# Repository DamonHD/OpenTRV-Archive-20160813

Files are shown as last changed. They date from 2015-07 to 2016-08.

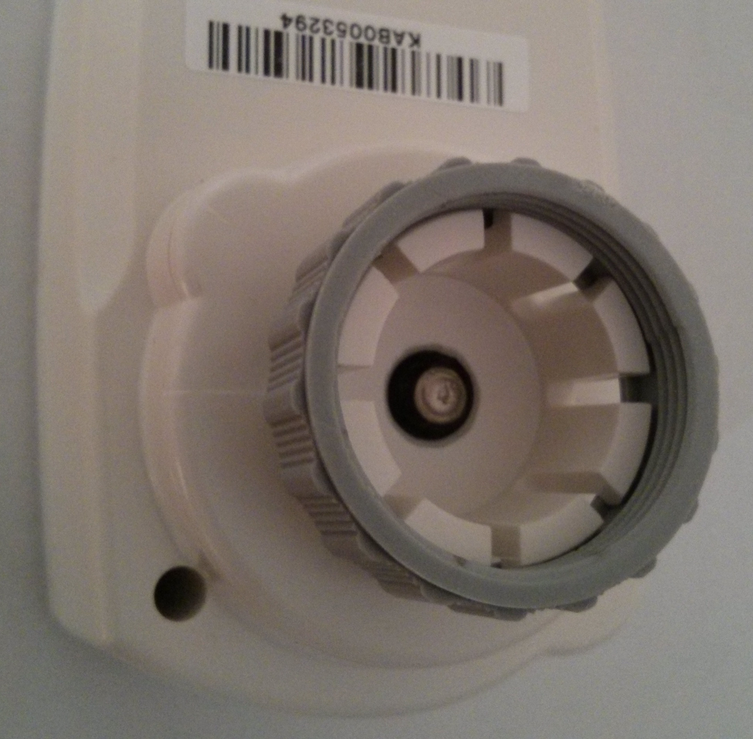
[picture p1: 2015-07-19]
docs/maker-fair-sandown-park/sources/rtrv.jpg

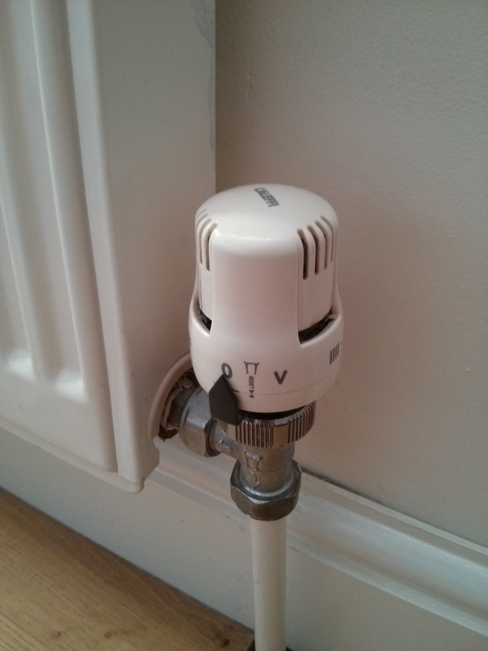
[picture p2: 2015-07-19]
docs/maker-fair-sandown-park/sources/IMG_20131211_112003.jpg

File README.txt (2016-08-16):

WARNING: AS OF 2016/08/13 THIS IS A READ-ONLY ARCHIVE/SNAPSHOT WITH HISTORY

See https://github.com/opentrv/OTWiki/wiki/Repo-Restructure-2016-08-13
for how the content has been refactored.

This is the OpenTRV (Open-Source Thermostatic Radiator Valve) project.

See http://www.earth.org.uk/open-source-programmable-thermostatic-radiator-valve.html for more.

Contains software and hardware elements.

Note that the content of this project is available under a permissive licence,
Apache 2.0 or (Solderpad 0.51 for hardware elements) unless otherwise stated,
and is provided supplied AS-IS with no warranties of any kind.

Fragments of contributed code, libraries, etc, within here may have their own licences,
in which case that should be explicit in each case.

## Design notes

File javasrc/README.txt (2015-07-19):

Installation instructions

To install on a Raspberry Pi, you will need to install the following
packages first:

$ sudo apt-get install librxtx-java
$ sudo apt-get install libjson-simple-java

The latest raspbian release (2015-02-06) comes with Oracle JDK 8 by default,
which should work. If you prefer 7, you can install that instead:

$ sudo apt-get install oracle-java7-jdk

Add the latest soft link in /usr/lib/jvm
$ cd /usr/lib/jvm
$ ln -s ./jdk-8-oracle-arm-vfp-hflt latest

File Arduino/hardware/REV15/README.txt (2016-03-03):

REV15+

A set of modular processor and sensor boards that can be stacked on top of each other as needed. These boards would have the I2CEXT connector, located in a common position.

The boards should include:
- A processor board.
- A power supply board.
- A radio board.
- Various sensor boards.

Specifications:

Physical layout:
- 5 cm x 5 cm form factor
- Standard positioning of 4 screw holes (as on REV2).
- Standoffs to work with connectors, long lead connectors.
- The I2CEXT connector as defined in https://github.com/DamonHD/OpenTRV/blob/master/standards/I2CEXT/tech-specs/201602-AVR-I2CEXT-connector.txt

Individual boards:
- Processor board (REV15):
    - Atmega328p
    - Watch xtal/resonator
    - Photodiode
    - Status LED
- Power supply board (REV16*):
    - Micro USB connector.
    - 2xAAA Battery connector (as on REV11)
    - 3.3 V regulator
- Radio board (REV17*):
    - Pads and connections for a single RFM23B or pin compatible RFM69.
    - Not backwards compatible with RFM22.
    - Decide on antenna.
- Sensor boards:
    - Temp/humidity (REV18*)
- More TBD. Suggestions include:
    - CO2 sensor board (sensor TBD).
    - PIR
    - CO
    - PMx
    - VO

* To be renamed.

Dir structure:
./
    - rev15.sch
    - rev15.brd
    - README.txt
    - CHECKLIST.txt
    + DRU+CAM/
    + gerbers/ *THIS CONTAINS GERBERS FOR ALL BOARDS*
    + REV16/
    + REV17/
    + REV18/

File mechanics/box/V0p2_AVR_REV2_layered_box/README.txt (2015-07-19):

Built around standard 5cm x 5cm board (with M3/3mm corner mounting holes, 1mm from edge).

M3 bolts with 30mm shank and full-height (2.4mm) nuts should then be correct length
with 0.5mm recess at top 30mm case height.

4 layers totalling 30mm:

0. (11mm) Base + screw mounts and lower collar with micro-usb cut-out.
1. (6mm) Top collar with power and boiler wire cut-outs.
2. (30.5mm-others) Spacer to provide clearance for front-panel items (and possibly to match bolt length!).
3. (3mm) Front panel with supports for button/LED/LDR board and cut-outs for those 4 items.

Good source of fasteners: www.westfieldfasteners.co.uk

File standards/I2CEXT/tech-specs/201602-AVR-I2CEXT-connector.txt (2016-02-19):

The OpenTRV project licenses this file to you
under the Apache Licence, Version 2.0 (the "Licence");
you may not use this file except in compliance
with the Licence. You may obtain a copy of the Licence at

http://www.apache.org/licenses/LICENSE-2.0

Unless required by applicable law or agreed to in writing,
software distributed under the Licence is distributed on an
"AS IS" BASIS, WITHOUT WARRANTIES OR CONDITIONS OF ANY
KIND, either express or implied. See the Licence for the
specific language governing permissions and limitations
under the Licence.

Author(s) / Copyright (s): Damon Hart-Davis 2014--2015

REVISIONS

2015/11/27: Revision 6 proposal, New I2CEXT design.
2014/09/14: Revision 5, adding some more details of location and form.
2014/09/08: Revision 4, allowing 4k7 for RX/TX serial for common values.
2014/09/08: Revision 3, note that the nIRQ and nSC lines can be left unconnected on some board variants.
2014/09/04: Revision 2, 14-pin connector, added nINT and nSC2 after dev mailing list suggestions
2014/09/03: Revision 1, 12-pin connector

Aim:

Trying to develop a simple I/O extension/shield system for OpenTRV to add more sensors (etc) easily.

Also this should allow an easy bridge to other systems such as RPi / BB / etc.

This must be simple and small and cheap enough to use in hobby / dev / prod environments and allow (in priority order):

1) I2C expansion.
2) In-Circuit Programming of AVR.
3) One-Wire expansion.
4) Serial off-take, eg for CLI interaction.

The connection should ideally be keyable or at least not cause instant destruction if reversed for example.

New Suggestion:

20 way (2x10) pin stackable

0.1 " pitch

Following pin pattern:
  PIN 1| PIN 2
MISO * .. * 3V3 (Vcc)
 SCK * .. * MOSI
nRST * .. * GND
 N/P X .. X N/P
 SCL * .. * GND
 SDA * .. * GND
nIRQ * .. * N/C
 nSS * .. * TX
  DQ * .. * RX
 PIO * .. * RTS

1) Pins 1-6 are standard AVR ICSP connections
2) 7-8 have no pins. This:
    a) Gives space for an IDC connector when programming with ICSP.
    b) Allows for a keyed 20 pin IDC.
3) 10-20 (even only) are standard FTDI connections (as on cable from RS components)
4) 9 & 11 are I2C connections.
5) 13 is a generic interrupt line to the AVR.
6) 15 is a slave select line in case of an external SPI peripheral. NOT the one connected to an on board radio module (if present).
7) 17 is a one wire serial connection.
8) 19 is a peripheral power enable line.

a) N/C means No Contact.
b) RX and TX are protected by 4K7 series resistors from AVR.
c) nRST (input to main board) is active low and is pulled up to 3V3/Vcc with 4k7--10K series resistor at AVR.
d) SCL and SDA are pulled up at AVR with 4K7 resistors to 3V3/Vcc.
e) 3V3 can be anywhere from 1V8 to 3V6 absolute; 2V to 3V6 operating.
f) nIRQ (input to main board) is active low and is pulled up to 3V3/Vcc with a 10K--47K nominal resistor and a 1K series resistor: this should be driven with open collector/drain driver only.
g) nSS (output from main board) is the active low select for an SPI device on the bus,
h) The nIRQ and nSS lines can be left unconnected unless the main board variant explicitly supports them.
i) N/P means No Pin.
j) PIO is connected to the IO_POWER_UP pin (via a resistor?) and is used for switching external sensors on
k) RTS is connected to nRST via a 100nF capacitor

Features:

1) Top 6 pins can be used directly with 6-pin AVR programmer.
2) 6 pins down the side can be used directly with a 6 pin FTDI cable (but must be powered from a different source)
3) When used with properly keyed IDC, cable cannot be inserted the wrong way.
4) The connector must be laid out as a single unit on the PCB ie. as a single 20 pin header
5) The connector may be populated by a 6 pin and a 12 pin header

Current:

14-way (2x6) pin stackable (pins or socket on board, suggestions please, RPi is pins).

0.1" pitch to be easy for DIY shields, eg with Veroboard as I just did for my RPi.

Following pin pattern:

MISO * .. * 3V3 (Vcc)
 SCK * .. * MOSI
nRST * .. * GND
nIRQ * .. * nSC
 SCL * .. * SDA
  RX * .. * TX
 N/C * .. * DQ

a) N/C means No Contact and can be used to key the connector.
b) RX and TX are protected by 10k series resistors from AVR.
c) nRST (input to main board) is active low and is pulled up to 3V3/Vcc with 4k7--10K series resistor at AVR.
d) SCL and SDA are pulled up at AVR with 4K7 resistors to 3V3/Vcc.
e) 3V3 can be anywhere from 1V8 to 3V6 absolute; 2V to 3V6 operating.
f) nIRQ (input to main board) is active low and is pulled up to 3V3/Vcc with a 10K--47K nominal resistor and a 1K series resistor: this should be driven with open collector/drain driver only.
g) nSC (output from main board) is the active low select for an SPI device on the bus,
h) The nIRQ and nSC lines can be left unconnected unless the main board variant explicitly supports them.

Features:

1) Top 6 pins can be used directly with 6-pin AVR programmer.
2) Rest of pins carry I2C (SDA, SCL), OneWire (DQ) and serial (RX, TX, protected by 10k series resistors)
3) If entire connector rotated boards unlikely to be destroyed instantly.

Bit more on (3): RX and TX are safe to short to GND or 3V3 or anything else, nRST safe to short to either rail, DQ/SCA/SCL safe to short to GND.

Connector form/style and location, and constraints:

1) Should be near board edge but not in corner for REV2-style 5x5 box.
2) Should be placed prob near edge for easy dev access with 3D-printed board.
3) Should allow USB micro socket to go back in its REV2 position if possible.
4) Should allow I2CEXT board on 5x5 footprint to also be RPi HAT board.
5) Must not be single-source nor expensive nor anywhere near end-of-life.

Some agreed details:

a) Male 7x2 0.1" pitch connector like top part of Raspberry Pi A/B/B+ GPIO connector, with pins above the board (component side).
b) Stacked board to have female connector below the board with extra long pins up.
c) Location on standard 5cm x 5cm OpenTRV board:
   6.35mm (left) x 2.375mm (down) from top left corner of board to centre of top-left pin (3V3)
   with the connector running left to right
   with pins pointing vertically away from the plane of the board towards the viewer.

Note: see alternatives such as http://www.tag-connect.com/ for SPI/ICP part.

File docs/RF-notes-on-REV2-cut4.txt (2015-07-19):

2014/07/03: discussing possible CE-stamp RF problems on IRC...

[21:40] mikestir    yes looking at it it's not great in terms of ground plane, but it's not exactly a speed demon
[21:41] mikestir    I can't see it being a big problem
[21:41] mikestir    also the rf track isn't
[21:41] mikestir    and the tracks are _still_ unnecessarily thin
[21:41] mikestir    I've given up telling you about that though
[21:42] DamonHD I did try to widen them a little but we were having trouble routing.
[21:42] DamonHD And all the supply tracks are now much wider than they were in their own net class.
[21:42] Boelle_DK   *me hides*
[21:42] DamonHD And we're way above iTEAD and PMS limits.
[21:43] mikestir    the ground plane thing just needs some stitching vias so you don't have it cut up into slots
[21:43] mikestir    slots are bad - they act as antennas
[21:43] DamonHD Doesn't that risk ground loops?
[21:43] mikestir    no - you have a ground loop as it is
[21:43] mikestir    look at that thin section of ground on the top layer that goes all the way around the bottom edge
[21:44] mikestir    if you have narrow sections like that and you can't stitch it you need to make sure there's a break at one end
[21:45] DamonHD So stitching / multiple routes is OK.
[21:45] DamonHD ?
[21:45] mikestir    yes
[21:45] DamonHD OK.
[21:45] DamonHD Good to know. Thanks.
[21:45] mikestir    what you don't want is a pair of ground tracks on either side with a via at each end
[21:45] mikestir    if you stick vias all the way along you don't have a loop any more
[21:46] mikestir    the vias and the tiny sections in between have such low resistance and inductance that they cease to matter
[21:47] mikestir    your antenna track should really be designed as a coplanar waveguide with stitching vias along the adjoining ground plane, but it's so short you probably don't need to care about that - what you have is probably fine

[21:47] DamonHD Good!
[21:48] mikestir    http://www.mike-stirling.com/gallery3/index.php/HAB/DSC_2396
[21:48] mikestir    look at the rf layout on that

[21:48] mikestir    that could probably use more stitching vias but I wanted to be kind to the fab, and it works fine

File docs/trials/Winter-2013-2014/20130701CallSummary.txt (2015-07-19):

DHD20130701

Summary of 09:30 telephone conference call today between:
Prof Ruth Rettie (RR) http://www.smartcommunities.org.uk/
Dr Kevin Burchell (KB) http://www.smartcommunities.org.uk/
Damon Hart-Davis (DHD) OpenTRV

DHD gave a brief summary of how the OpenTRV device behaves (eg FROST/WARM/BAKE modes and LEARN),
and explained that it had some additional optional anticipatory 'smarts' that could be used/disabled.

DHD is very keen to get some sort of objective metrics to DECC by end of 2013/2014 winter
to help DECC decide ASAP if worth pursuing zoned smart heating with market incentives etc, etc.

RR suggested that we wouldn't have enough people or time for a full controlled trial
getting good estimates of energy savings, partly because interacting with householders
(eg just talking to them, or collecting gas meter reading)
is slow and expensive and distorts results.

We agreed that we want to have 'normal' people in the trial,
since the aim of OpenTRV is to make energy saving (and decent comfort)
simple/easy (no complex controls/programming) for non-techie non-energy-fanatics,
with relatively little explicit interaction with their heating system.

DHD would also like to include OpenTRV and SuperHome people in the trial,
at least on the side, as OpenTRV should also work for the energy-aware
and/or energy-efficient homes.

RR suggested that we doing a small rolling trial and not expect too many hard numbers,
looking first to improve the ergonomics and to test people's reactions to OpenTRV
in a small set of homes, eg including KB's.  Do people like it?  Do they use more heating?

(This initial set/period might be DHD + KB + BG + BH + maybe one or two others.) 

This can be started before winter proper to test the controls,
but raising the programmed temperature thresholds.

Then maybe we rope in a few of the Smart Communities participants.

DHD would still like to look for a drop in kWh/HDD after OpenTRV installation,
eg in households doing monthly or weekly gas meter readings.

(We might possibly expand to another 5--10 households for the second period?)

RR suggested that the way to take this forward might be with TSB
(Technology Strategy Board) money with a firm to commercialise
one version of OpenTRV (which the permissive licences are meant to facilitate).

We might also talk to Alex at Southampton.

We'll get the first phases going and tighten up subsequent trial design
as we go along, but keeping an eye on getting objective metrics whenever possible.

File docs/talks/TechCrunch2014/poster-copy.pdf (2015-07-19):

£100 per home is our target to fix it

In passing we have created an open, cheap, reliable, low-power

Cheap as chips can be
it must be IoT
(in a speech bubble,
something more
pithy?)

£6bn Is needlessly paid to energy companies in the UK annually

UK houses extant

in 2050 26.5m

OpenTRV
From Rads to (IoT Data) Riches
60%

# half wasted!

of typical UK home energy bill and carbon footprint*
is for space heating
which is
as much as

with radio, security,
and even energy harvesting under development,
for fit-and-forget, cheap-as-chips!

*10% of UK footprint, 8% of EU

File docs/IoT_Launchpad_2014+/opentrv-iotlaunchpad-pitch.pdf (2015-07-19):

w | opentrv.org.uk
t | @opentrv
e | opentrv@opentrv.org.uk

# openTRV

# sensors and infrastructure cheap 'n' easy Damon Hart-Davis

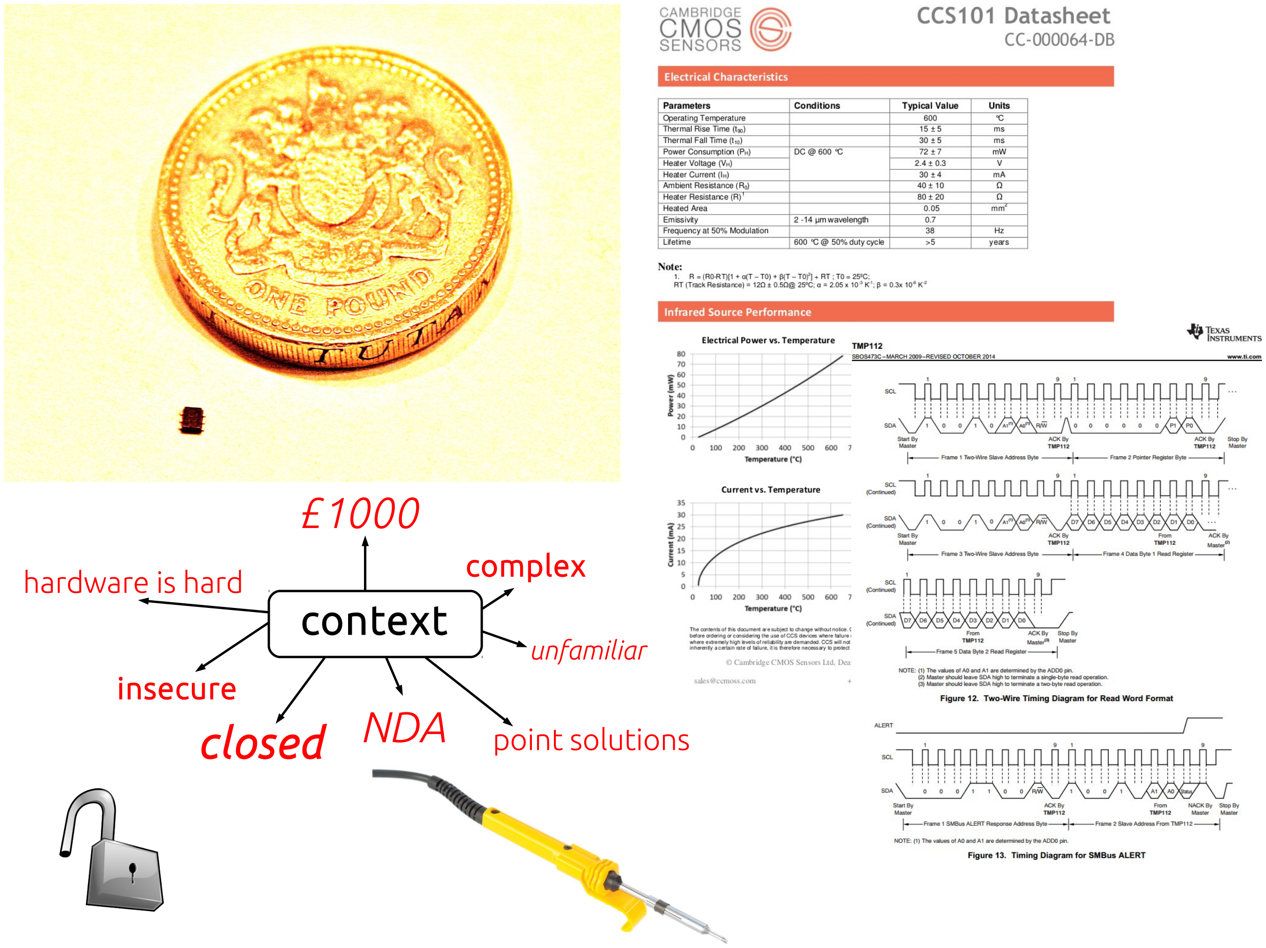
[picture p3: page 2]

## context

insecure

hardware is hard

## closed

£1000

complex

NDA point solutions

unfamiliar

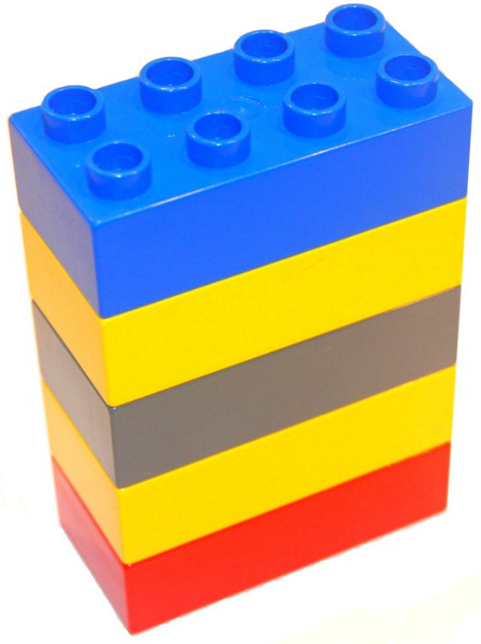
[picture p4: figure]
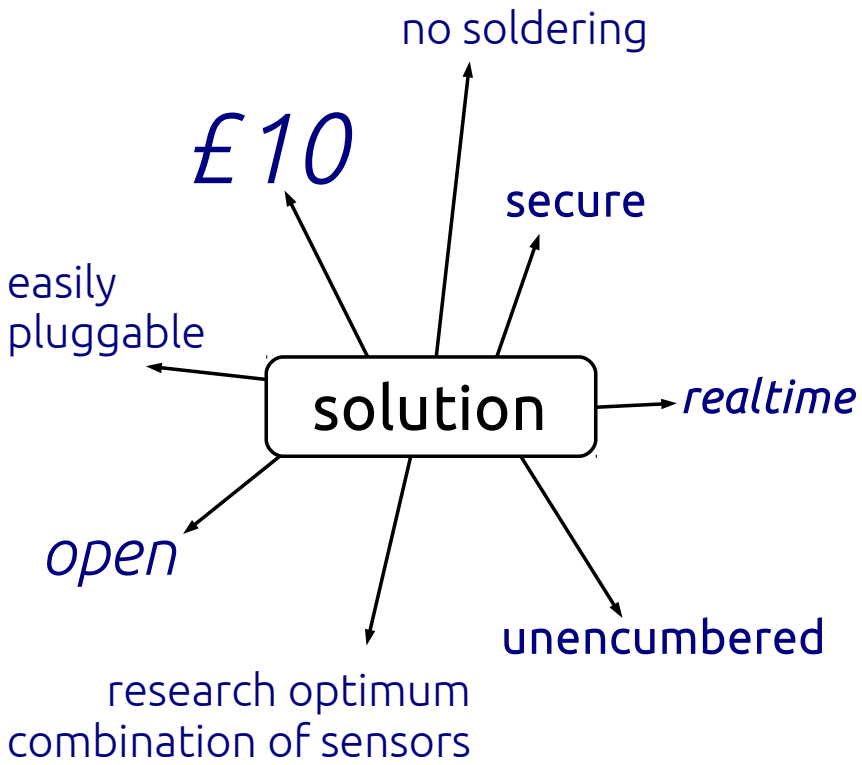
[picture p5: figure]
solution; unencumbered; open; no soldering; secure; research optimum combination of sensors; easily pluggable; realtime

## customer acquisition

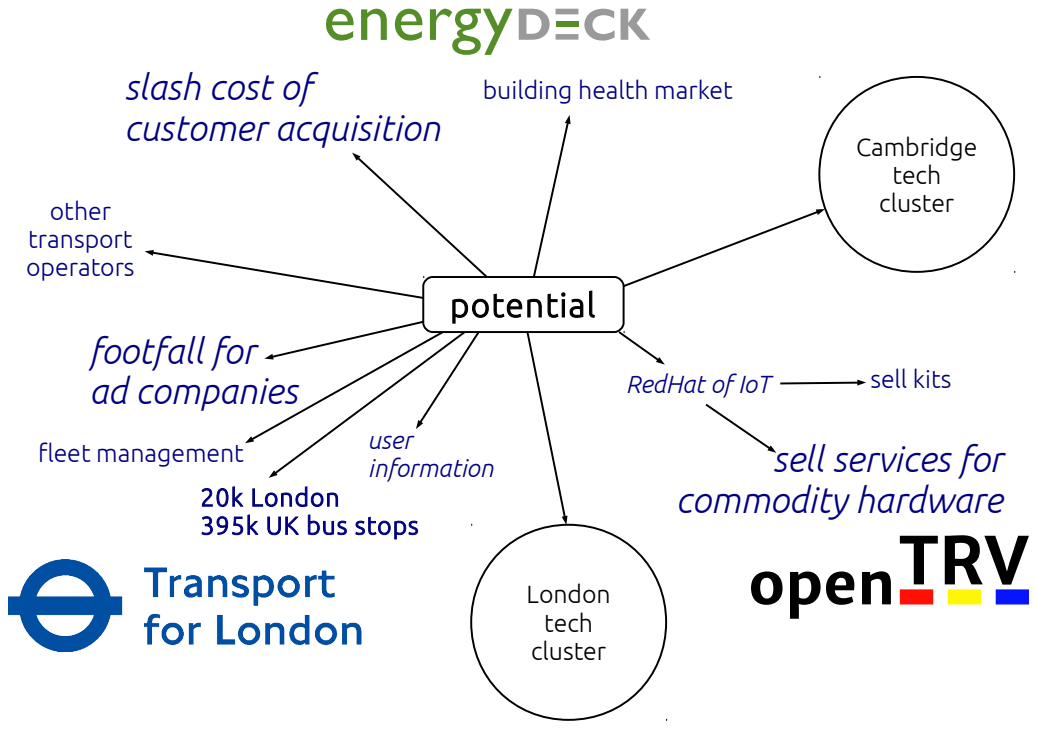
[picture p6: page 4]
potential; slash cost of; building health market; other transport operators; Cambridge tech cluster; London tech cluster; user information; footfall for ad companies; fleet management

RedHat of IoT

sell kits
sell services for
commodity hardware
openTRV

20k London
395k UK bus stops

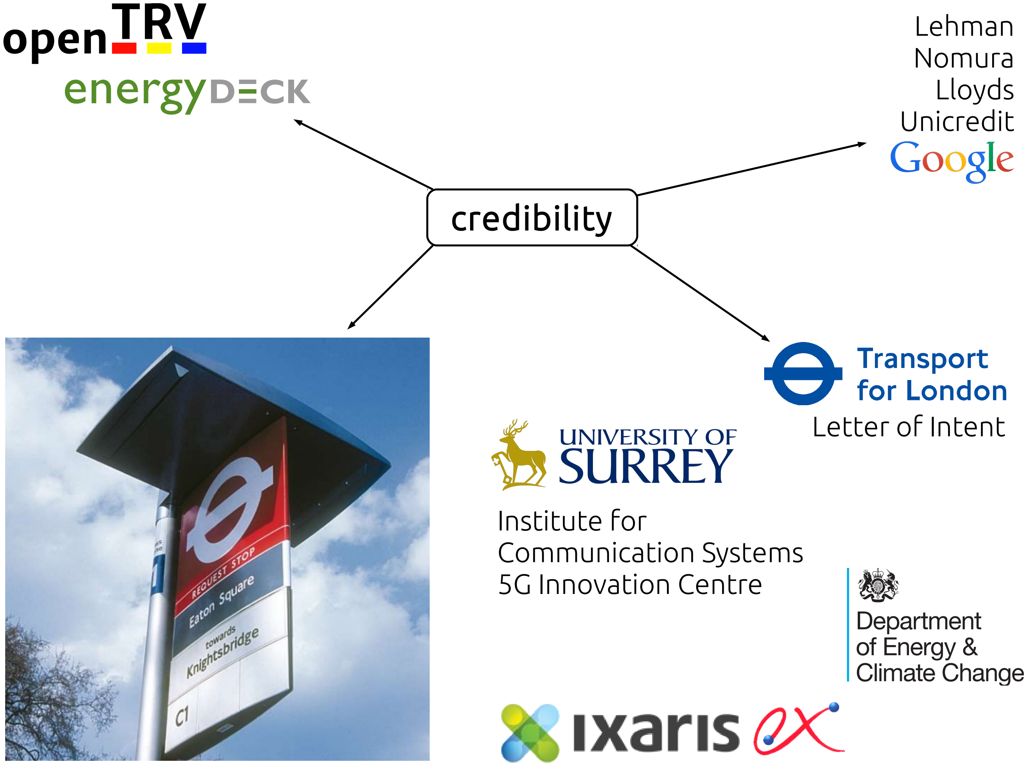
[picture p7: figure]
openTRV; Institute for Communication Systems 5G Innovation Centre; Letter of Intent; Lehman Nomura Lloyds Unicredit; credibility

£

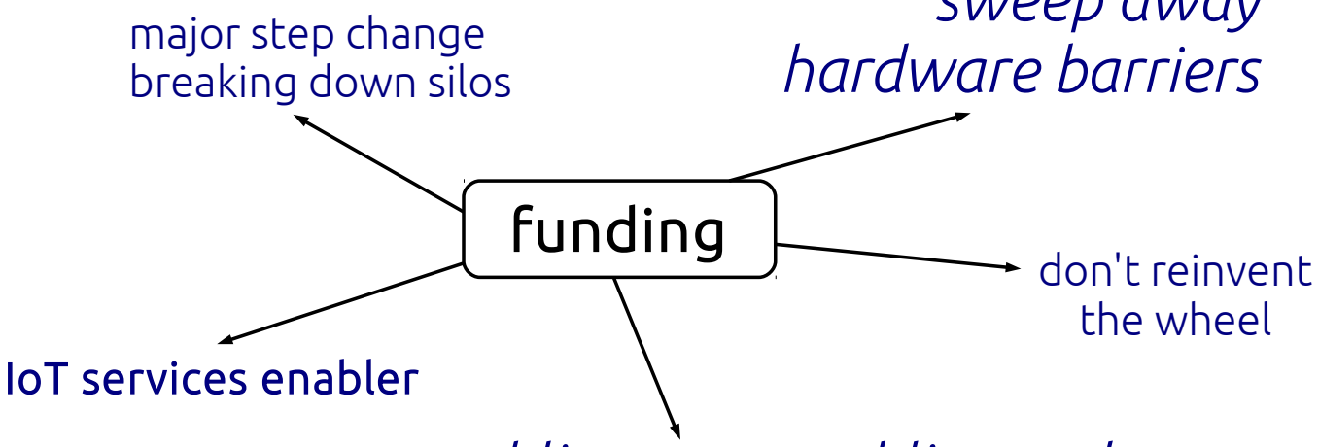
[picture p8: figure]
funding; IoT services enabler; major step change breaking down silos; hardware barriers; don't reinvent the wheel

## public money public good

## sweep away

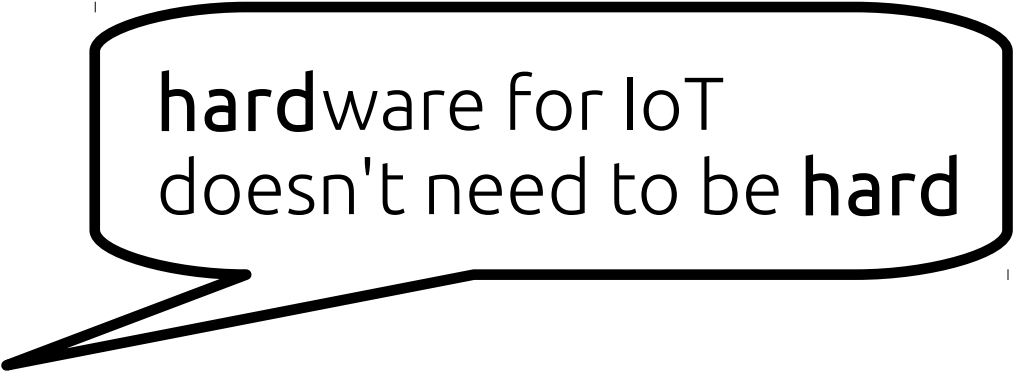
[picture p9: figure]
hardware for IoT doesn't need to be hard
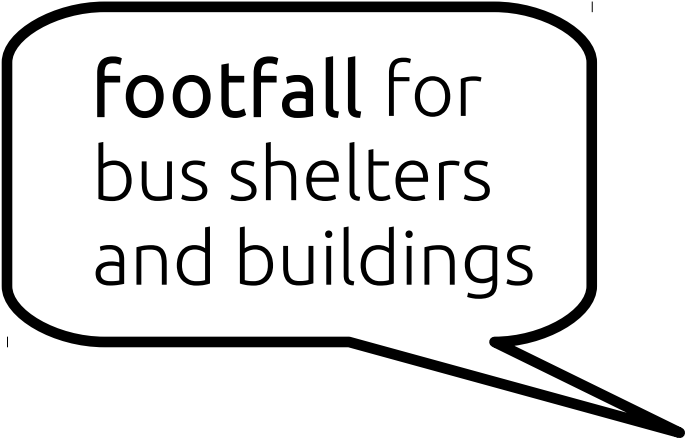
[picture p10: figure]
footfall for bus shelters and buildings
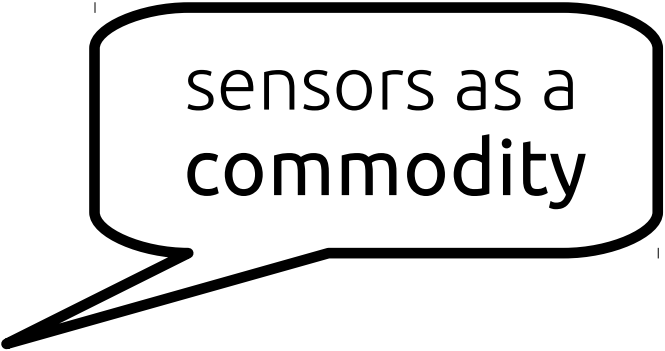
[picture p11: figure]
sensors as a commodity
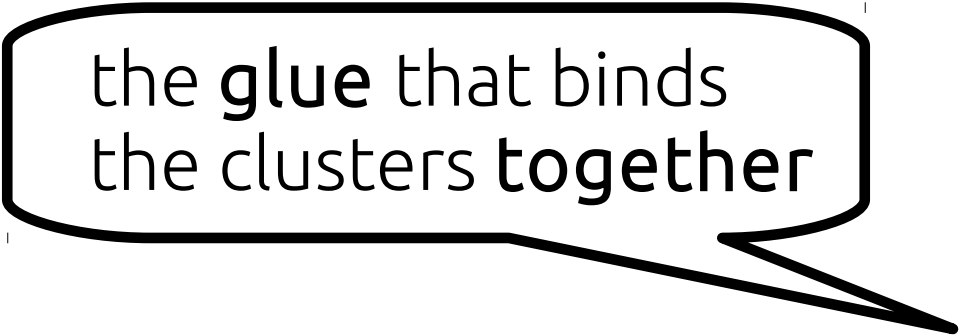
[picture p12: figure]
the glue that binds the clusters together

## hardware for IoT doesn't need to be hard

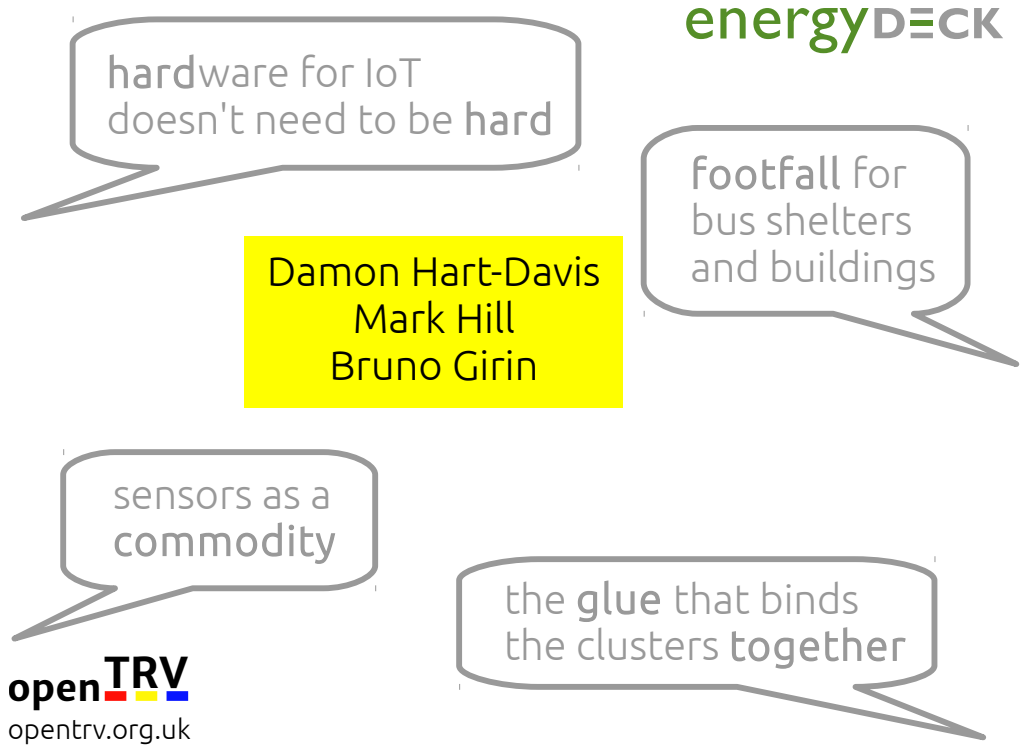
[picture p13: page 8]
footfall for bus shelters and buildings; sensors as a commodity; openTRV

Damon Hart-Davis
Mark Hill
Bruno Girin

the glue that binds
the clusters together

opentrv.org.uk

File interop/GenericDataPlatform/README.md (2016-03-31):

# Generic data platform interop

The aim of this section is to provide a proof of concept for interoperability
with a generic data platform. It comes in thee parts:

1. A data platform proof of concept that would be deployed on a cloud server
   and that offers a REST API. Note the the implementation provided here is
   a proof of concept and is not designed to support large volumes of data.
2. A bridge component that would be deployed on the OpenTRV concentrator
   and would send data to the data platform in a way that this platform can
   understand.
3. Library code shared by both the platform and the bridge.

The platform and bridge implement a simple provisioning protocol that works as
follows, where:

- `init` is a well known URL on the platform;
- `uuid` is the unique identifier of the bridge / concentrator, can typically
  be the MAC address;
- `data` is sensor data in SenML format.

The current interaction doesn't include the ability to exchange configuration
options between the bridge and the platform.

    Bridge                                                      Platform
    ------                                                      --------
       |    1. GET init                                             |
       |----------------------------------------------------------->|
       |                                   Commissioning URL (comm) |
       |<-----------------------------------------------------------|
       |                                                            |
       |    2. POST comm, uuid                                      |
       |----------------------------------------------------------->|
       |                                          Message URL (msg) |
       |<-----------------------------------------------------------|
       |                                                            |
    +------ 3. Repeat -------------------------------------------------+
    :  |                                                            |  :
    :  |    3.1. POST msg, data                                     |  :
    :  |----------------------------------------------------------->|  :
    :  |                                                            |  :
    +------------------------------------------------------------------+
       |                                                            |

1. bridge GETs well know initialisation URL on platform; the platform replies
   with a JSON object that includes a commissioning URL
2. bridge POSTs key info, including UUID to platform commissioning URL;
   platform replies with a JSON object that includes a message posting URL
3. bridge POSTs data frames in SenML format to the message URL

The platform makes all collected data available over a REST API that follows
the Hypercat standard and as such provides a minimal implementation of the
standard.

## Suggested extensions

At the moment, the bridge does not have to remember the message URL, it can
just re-commission. The side effect of this is that another bridge could POST
to the commissioning URL with the same UUID and be able to masquerade as the
first bridge. To prevent this, we could add the following extensions:

- prevent re-commissioning, thus forcing the bridge to remember the
  commissioning parameters
- exchange security keys on steps 3 and 4 to enable data signing for step 5,
  if connection is over HTTPS

From a functional perspective, useful extensions of this mechanism would be:

- Include in the response to the `init` call all the generic platform options,
  including a pointer to the Hypercat root catalogue;
- Include in the response to the `comm` call all device specific options
  including initial configuration, device update processes (e.g. Ubuntu Snappy
  store), etc;
- Add a set of configuration exchange processes modelled on TR-069 to enable
  the device or the platform to exchange configuration options and make it
  possible for the platform to request a configuration change.

## Run the tests

You can run all unit tests by calling the following command in the same
directory as this file:

    python3 -m unittest discover

## Run the code

The easiest way to run the code for testing is in a `vagrant` virtual machine.
This is managed by the `Vagrantfile` at the root of the repository. Start
the VM and connect to it:

    vagrant up
    vagrant ssh

Start the platform component:

    python3 -m opentrv.platform

Start the bridge concentrator component:

    python3 -m opentrv.concentrator

## Install the code

You can install the code on a clean VM or a RaspberryPi by running the install
script located in the `vm` folder:

    bash wm/install.sh

This will install all dependencies, as well as the `mosquitto` MQTT broker.
if you want to install only the Python code, you can install an editable
version by running the following command:

    sudo pip3 install -e .

When installed this way, any change in the code directory will be picked up
immediately, which also means that if the repository is removed, the code will
stop working. If you'd rather install it permanently, you can use the
following command:

    sudo pip3 intall .

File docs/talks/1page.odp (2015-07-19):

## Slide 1

open source

open hardware

60%

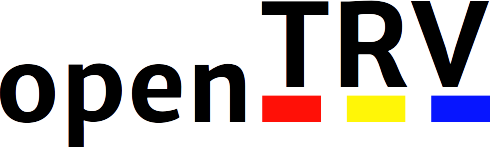
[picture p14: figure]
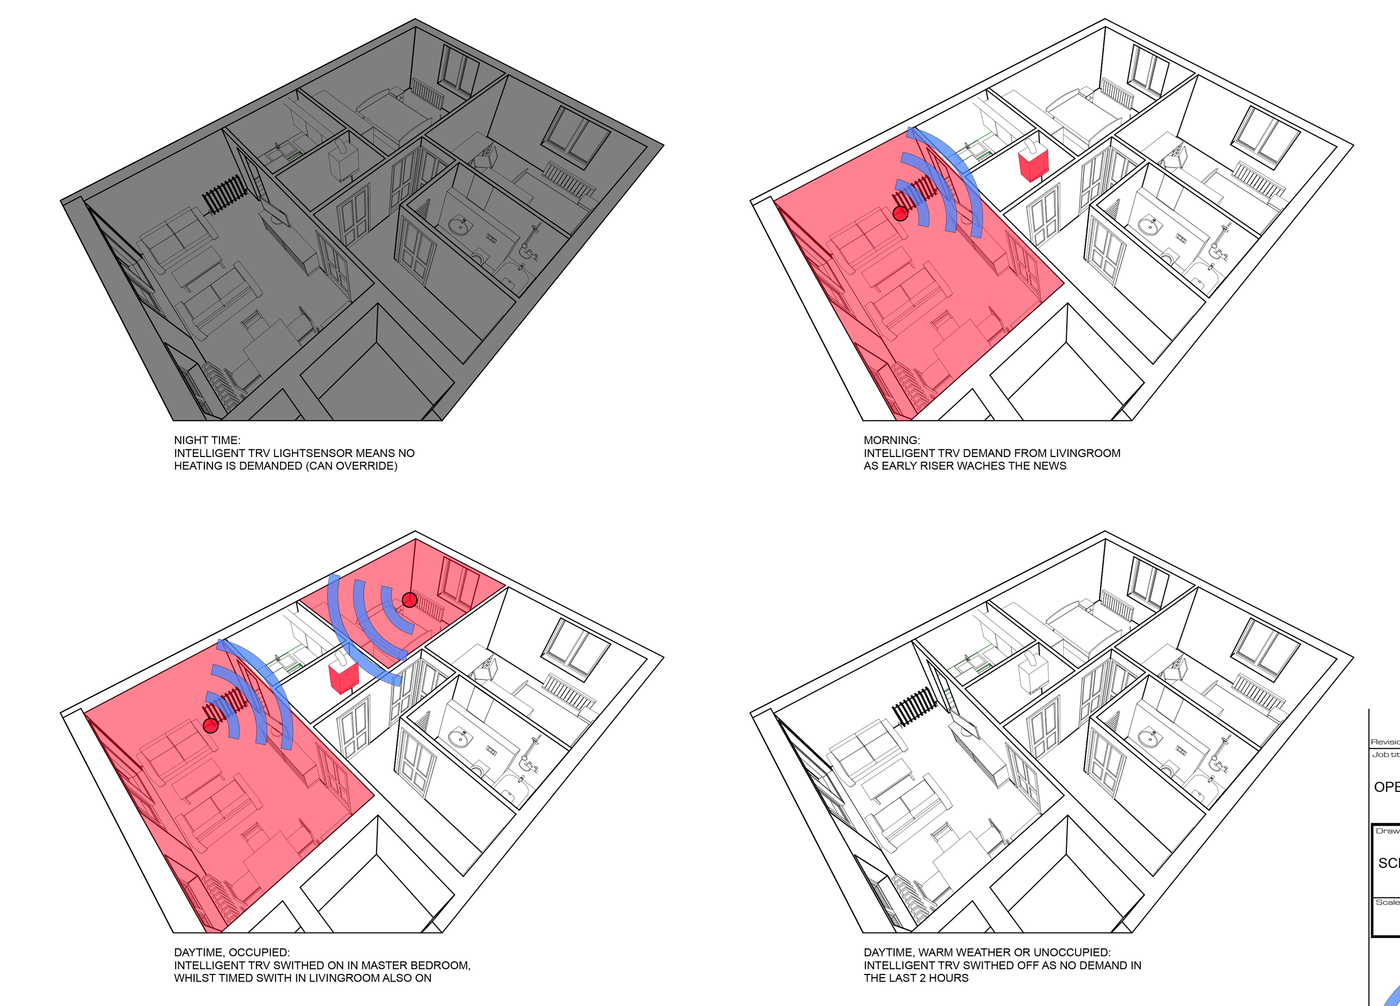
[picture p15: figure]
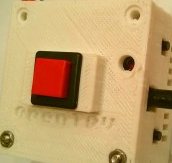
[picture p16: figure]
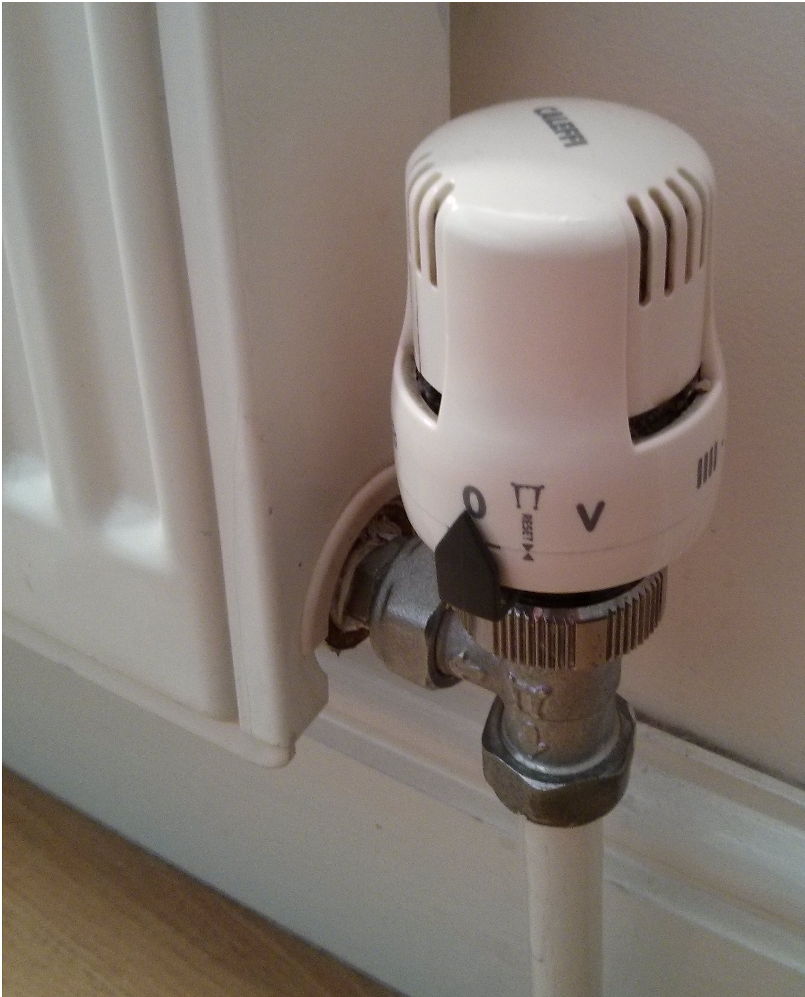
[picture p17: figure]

10%

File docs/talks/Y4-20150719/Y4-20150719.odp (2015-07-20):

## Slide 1

Y4: CO2, PV, IoT!

What a Mouthful!

w opentrv.org.uk

t @opentrv

Damon Hart-Davis

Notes: OpenTRV are leading an Innovate UK funded project to sense footfall in bus shelters and buildings, and will demonstrate the impact of IoT when it becomes ubiquitous, easy to use and produces real world results. 15m “How do we generate enough connectivity and data to develop a truly “smart” built environment? Pioneers in this field discuss how IOT technology is increasingly being embedded in our built environment. The benefits to be gained from this data will be explained– from energy efficiency, to remote maintenance to better health. How is the data brought together and made sense of? Are there security risks?”

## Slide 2

SOLAR PV

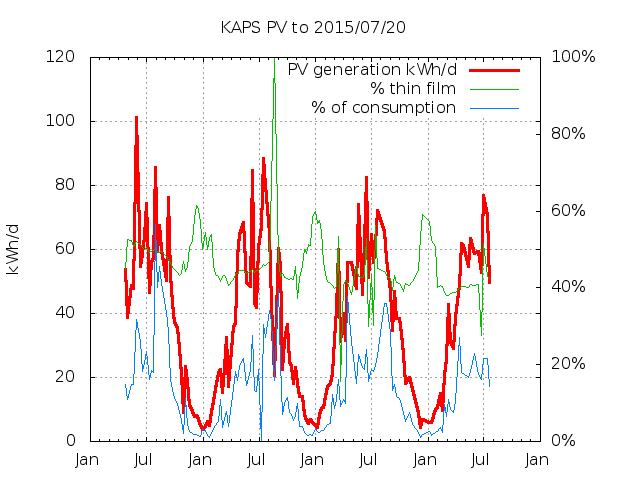
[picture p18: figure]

Solar PV: about 10% of the school's electricity use

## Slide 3

SOLAR PV

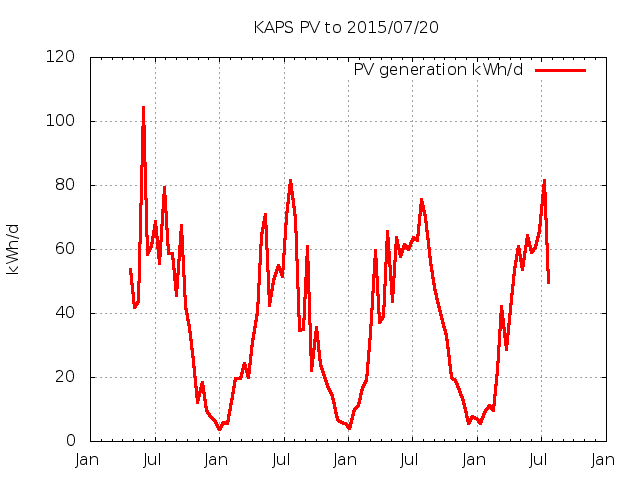
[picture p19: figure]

Solar PV: about 10% of the school's electricity use

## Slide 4

SNOOZING

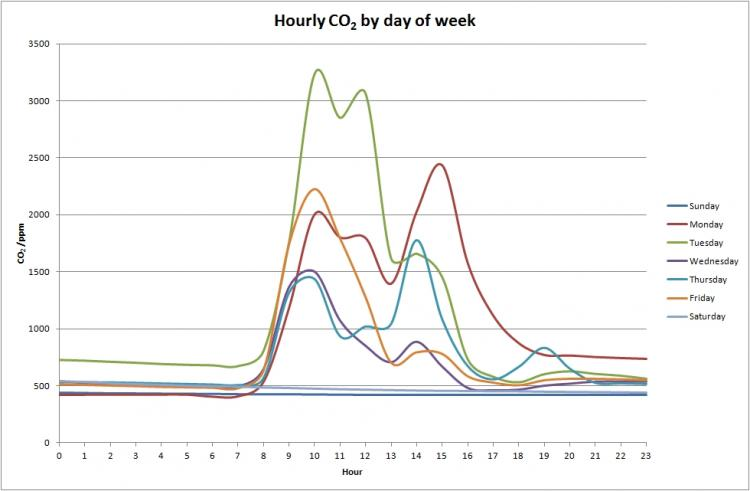
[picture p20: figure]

Problem: falling asleep because of high CO2 levels?

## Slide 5

PROBLEM

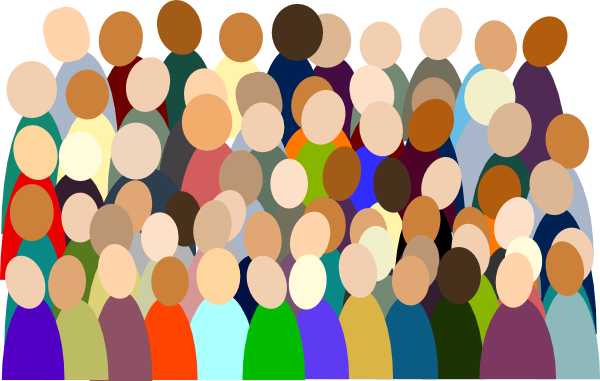
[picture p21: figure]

?

Problem: operator knows where buses are, but what about the people waiting?

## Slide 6

Problem: UK carbon emissions from domestic space heat 20%, gas bill £10bn/y, 50% wasted.

PROBLEM

UK carbon emissions

20%

home heat

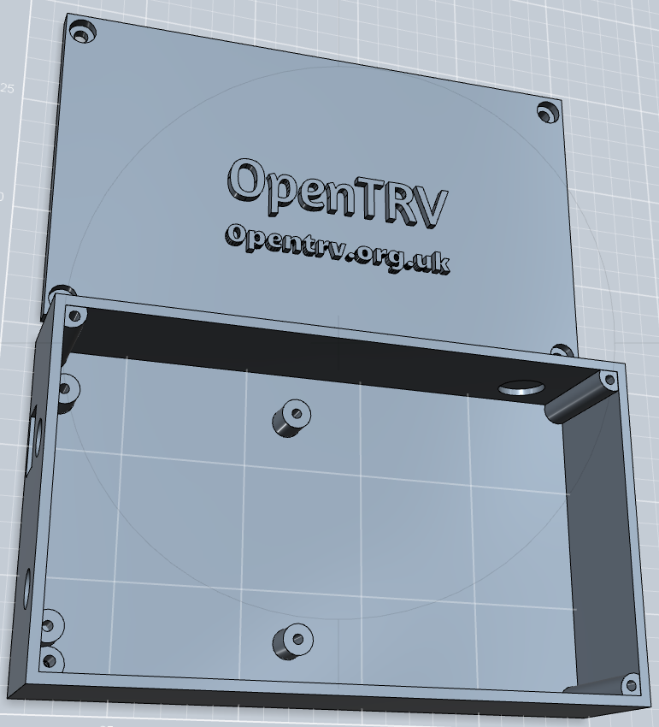
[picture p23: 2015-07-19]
mechanics/box/roughs/Case 2 Screenshot.png

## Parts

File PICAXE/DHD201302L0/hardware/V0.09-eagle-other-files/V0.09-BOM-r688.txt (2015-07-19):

Stereo Jack  SC1488-1-ND     0.44 £
Power Jack   CP-002APJCT-ND  1.22 £
3.3V Regulator   TC10553.3VCT713CT-ND   0.31 £
PicAXE 18M2+     AXE015M2SM 2.64 £   techsupplies.co.uk
DS1306   DS1306E+-ND     4.08 £
RFM22B   RFM22B-868-S1   9.28 £  uk.farnell.com
10 uF    478-4086-1-ND   0.37 £
10 Kohm  RHM10KGCT-ND    0.07 £
22 Kohm  RHM22KACT-ND    0.07 £
4.7 Kohm     RHM4.7KECT-ND   0.07 £
LED1     67-1656-1-ND    0.44 £
LED2     67-1684-1-ND    0.44 £
100 nF   445-2287-1-ND   0.24 £
100 uF   587-1349-1-ND   1.22 £
100 pF   478-3717-1-ND   0.11 £
100 Kohm     RHM100KECT-ND   0.07 £
470 Ohm  RHM470ERCT-ND   0.07 £
Crystal  644-1171-1-ND   0.94 £
0.1 F    604-1169-1-ND   3.53 £

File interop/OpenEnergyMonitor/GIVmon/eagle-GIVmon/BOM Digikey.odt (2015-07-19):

R1 470 Kohm 1/2 W PPCHJ470KCT-ND (http://www.digikey.co.uk/product-detail/en/HVR3700004703JR500/PPCHJ470KCT-ND/719656) 0,58 £ 0,68 $ 0,55 €

R2,R4,R5,R12,R13,R14 2,2 Mohm 1/4 W 2.2MGACT-ND (http://www.digikey.co.uk/product-detail/en/HHV-25FR-52-2M2/2.2MGACT-ND/2813167) 0,32 £ 0,46 $ 0,37 €

R15 10 Ohm 1/2 W NFR25H0001009JR500 (http://www.digikey.co.uk/product-detail/en/NFR25H0001009JR500/PPC10BCT-ND/614245) 0,33 £ 0,47 $ 0,38 €

R6, R9 39 Kohm 1/4 W 39KADCT-ND (http://www.digikey.co.uk/product-detail/en/MFP-25BRD52-39K/39KADCT-ND/2059135) 0,52 £ 0,55 $ 0,60 €

R8 120 Ohm 1/4 W 120ADCT-ND (http://www.digikey.co.uk/product-detail/en/MFP-25BRD52-120R/120ADCT-ND/2059115) 0,52 £ 0,55 $ 0,60 €

R10, R11 470 Kohm 1/4 W PCQJ470KCT-ND (http://www.digikey.co.uk/product-detail/en/HVR2500004703JR500/PPCQJ470KCT-ND/719631) 0,33 £ 0,54 $ 0,44 €

R7 10 Ohm 1/2 W PPC10.0XCT-ND (http://www.digikey.co.uk/product-detail/en/SFR16S0001009FR500/PPC10.0XCT-ND/594697) 0,16 £ 0,23 $ 0,19 €

R3 47 Ohm 1/2 W S47HCT-ND (http://www.digikey.co.uk/product-detail/en/CFM12JT47R0/S47HCT-ND/2617622) 0,08 £ 0,11 $ 0,09 €

D1,D2,D3,D4 1N4007 1N4007FSCT-ND (http://www.digikey.co.uk/product-detail/en/1N4007/1N4007FSCT-ND/965481) 0,10 £ 0,14 $ 0,11 €

Z1 1N5927B 1N5927BGOS-ND (http://www.digikey.co.uk/product-detail/en/1N5927BG/1N5927BGOS-ND/1474279) 0,30 £ 0,43 $ 0,35 €

C1 0,47uF 300V 399-5985-ND (http://www.digikey.co.uk/product-detail/en/R463N347000N0K/399-5985-ND/2704639) 0,51 £ 0,73 $ 0,59 €

C4 330uF 35V P5167-ND (http://www.digikey.co.uk/product-detail/en/ECA-1VM331/P5167-ND/245026) 0,29 £ 0,41 $ 0,33 €

C5 100pF 445-4726-ND (http://www.digikey.co.uk/product-detail/en/FK28C0G1H101J/445-4726-ND/2050075) 0,20 £ 0,29 $ 0,24 €

C2,C3 0,1uF 445-5258-ND (http://www.digikey.co.uk/product-detail/en/FK28X7R1H104K/445-5258-ND/2256738) 0,20 £ 0,29 $ 0,24 €

IC2 Dual Op-Amp 497-7683-5-ND (http://www.digikey.co.uk/product-detail/en/TS912IN/497-7683-5-ND/1040340) 1,09 £ 1,56 $ 1,27 €

IC1 5V Regulator LM78L05ACZNS/NOPB-ND (http://www.digikey.co.uk/product-detail/en/LM78L05ACZ%2FNOPB/LM78L05ACZNS%2FNOPB-ND/6333) 0,45 £ 0,65 $ 0,53 €

IC3 Optocoupler 751-1292-5-ND (http://www.digikey.co.uk/product-detail/en/IL300/751-1292-5-ND/1731525) 3,12 £ 4,43 $ 3,60 €

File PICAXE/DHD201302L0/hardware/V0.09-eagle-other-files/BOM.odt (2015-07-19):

*Stereo Jack SC1488-1-ND 0.44 £ *1 0.44

*Micro USB B 609-4613-1-ND 0.32 £ *1 0.32

*3.3V Regulator TC10553.3VCT713CT-ND 0.31 £ *1 0.31

*DS1306 DS1306E+-ND 4.08 £ *1 4.08

*RFM22B RFM22B-868-S1 9.28 £ *1 9.28

*10 uF 445-4112-6-ND 0.22 £ *2 0.44

*10 Kohm RHM10KGCT-ND 0.07 £ *1 0.07

*22 Kohm P22KADCT-ND 0.17 £ *1 0.17

*4.7 Kohm P4.7KADCT-ND 0.17 £ *7 1.19

*LED2 67-1684-1-ND 0.44 £ *1 0.44

*100 nF 399-1099-6-ND 0.07 £ *3 0.21

*100 uF 587-1349-1-ND 1.22 £ *1 1.22

*100 pF 478-3717-1-ND 0.12 £ *1 0.12

*100 Kohm 541-100KSACT-ND 0.15 £ *1 0.15

*470 Ohm RHM470DCT-ND 0.07 £ *1 0.07

*Crystal 644-1171-1-ND 0.94 £ *1 0.94

*LED1 751-1116-ND 0.52 £ *1 0.52

*DS18B20 DS18B20+T&RCT-ND 3.34 £ *1 3.34

*Screw Terminal 2 pin A98036-ND 0.35 £ *1 0.35

*Pin Headers 32 pins SAM1111-32-ND 4.75 £ *1 4.75 SAM1121-32-ND

LDR SEN002 0.29 £ *1 0.29 techsupplies.co.uk

PicAXE 18M2+ AXE015M2SM 2.64 £ *1 2.64 techsupplies.co.uk

Push Button GH7480-ND 2.17 £ *1 2.17

0.1 F 604-1169-1-ND 3.67 £ *1 3.67

Total approx 37,18

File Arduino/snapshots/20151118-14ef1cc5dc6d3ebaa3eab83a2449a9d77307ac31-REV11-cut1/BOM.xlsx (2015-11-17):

# of boards ttl |  |  |  |  |  |  | 30 | Black MEANS OK | RED MEANS OUT OF STOCK |  | Comments
 |  |  |  |  |  |  |  | Awaiting review | ONLY 5 IN STOCK
Quantity per board | Need to order | Min order | Unit price | Line Total | Seller Stock No | Manufacturer | Manufacturer Part. No. | Description | Legend | Supplier |  | Direct Link
10 | 300 | 50 | 0.028 | 8.4 | 213-2367 | TE Connectivity | CRG0603F4K7 | 4.7Kohm | R4, R5, R2, R9, R12, R6, R8 | RS Components |  | http://uk.rs-online.com/web/p/surface-mount-fixed-resistors/2132367
1 | 30 | 50 | 0.027 | 0.81 | 213-2531 | TE Connectivity | CRG0603F100K | 100Kohm | R1 | RS Components |  | http://uk.rs-online.com/web/p/surface-mount-fixed-resistors/2132531
2 | 60 | 50 | 0.028 | 1.68 | 213-2222 | TE Connectivity | CRG0603F470R | 470ohm | R7 | RS Components |  | http://uk.rs-online.com/web/p/surface-mount-fixed-resistors/2132222
2 | 60 | 50 | 0.006 | 0.36 | 213-2266 | TE Connectivity | CRG0603F1K0 | 1Kohm | R10 | RS Components |  | http://uk.rs-online.com/web/p/surface-mount-fixed-resistors/2132266
5 | 150 | 25 | 0.022 | 3.3 | 264-4630 | Kemet | C0603C104K4RAC | 100nF | C11, C7, C9, C10, C12 | RS Components |  | http://uk.rs-online.com/web/p/ceramic-multilayer-capacitors/2644630
1 | 30 | 50 | 0.026 | 0.78 | 464-6391 | AVX | 06035A101JAT2A | 100pF | C4 | RS Components |  | http://uk.rs-online.com/web/p/ceramic-multilayer-capacitors/4646391
1 | 30 | 10 | 0.215 | 6.45 | 885-1897 | Murata | GRM31CD80J107ME39L | 100uF | C8 | RS Components |  | http://uk.rs-online.com/web/p/ceramic-multilayer-capacitors/8851897/
1 | 30 | 5 | 0.824 | 24.72 | 667-6120 | EPSON TOYOCOM | MC-306, 32.768kHz, 20ppm, 6pF | Crystal | Q1 | RS Components |  | http://uk.rs-online.com/web/p/crystal-units/6676120
2 | 60 | 5 | 0.191 | 11.46 | 1328308 | Vishay | TLMS1000-GS08 | LED RED | LED | Farnell |  | http://uk.farnell.com/vishay/tlms1000-gs08/led-0603-red-4mcd-628nm/dp/1328308
1 | 30 | 10 | 0.293 | 8.79 | 700-0776 | Vishay | TEPT4400 | 60° Visible Light Phototransistor | PHT | RS Components |  | http://uk.rs-online.com/web/p/phototransistors/7000776/
1 | 30 | 1 | 2.530 | 75.9 | 696-3092 | Atmel | ATMEGA328P-AU | ATmega328P-AU | IC1 | RS Components |  | http://uk.rs-online.com/web/p/microcontrollers/6963092/
1 | 30 | 1 | 3.600 | 108 | RFM23-868-S1 | HopeRF | RFM23-868-S1 | RFM23B | RFM23 | Ideetron |  | http://www.hoperf.nl/RFM23B
1 | 30 | 1 | 0.600 | 18 | 2356198 | Wurth Elektronik | 61301421021 | Right Angle 14 Pin connector | IC2_EXT | Farnell |  | http://uk.farnell.com/wurth-elektronik/61301421021/header-2-54mm-pin-tht-r-a-14way/dp/2356198
0.34 | 10.2 | 10 | 0.683 | 6.9666 | 251-8351 | RS | W81136T3816RC | 12 Pin Header | JP1 | RS Components | Cut 36 in bits of 12 | http://uk.rs-online.com/web/p/pcb-headers/2518351/
1 | 30 | 1 | 2.820 | 84.6 | 1855468 | Sensiron | SHT21 | SHT21 | U1 | Farnell |  | http://uk.farnell.com/sensirion/sht21/sensor-humidity-temp-3x3mm-2/dp/1855468
1 | 30 | 1 | 0.187 | 5.61 | 18-2925 | Trupower | BH-421-3P | Battery Holder |  | Rapid Online |  | http://www.rapidonline.com/Electrical-Power/TruPower-BH-421-3P-2-X-AAA-PCB-Battery-Holder-18-2925
1 | 30 |  |  |  |  |  |  | PCBs |  | ?
 | Total: |  |  | 365.83
 | Each board: |  |  | 12.19
Out of stock
1 | 30 | 5 | 0.710 | 21.3 | 749-2059 | Murata | GRM31CR60G107ME39L | 100uF | C8 | RS Components |  | http://uk.rs-online.com/web/p/ceramic-multilayer-capacitors/7492059
2 | 60 | 100 | 0.127 | 7.62 | 888-6029 | Lumex | SML-LX0603SIW-TR | LED RED | LED | RS Components |  | http://uk.rs-online.com/web/p/visible-leds/8886029/
1 | 30 | 5 | 1.008 | 30.24 | 4681350 | Molex | 90122-0767 | Right Angle 14 Pin connector | IC2_EXT | RS Components |  | http://uk.rs-online.com/web/p/pcb-headers/4681350/

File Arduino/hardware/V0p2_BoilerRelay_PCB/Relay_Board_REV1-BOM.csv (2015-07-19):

# of boards ttl |  |  |  | 5 | PURPLE MEANS OK
Quantity per board | Need to order | Seller Stock No | Manufacturer | Manufacturer Part. No. | Description | Legend | Supplier | Direct Link
1 | 5 | 714-2334 | FCI | 10103592-0001LF | Micro USB socket | USBPOWER | RS Components | http://uk.rs-online.com/web/p/micro-usb-connectors/7142334/
2 | 10 | 220-4260 | Phoenix Contact | MPT 0.5/ 2-2.54 | Screw Terminal 2-way | X1, X2 | RS Components | http://uk.rs-online.com/web/p/pcb-terminal-blocks/2204260
1 | 5 | 710-0104 | TE Connectivity | 282834-2 | Screw Terminal 2-way | X3 | RS Components | http://uk.rs-online.com/web/p/pcb-terminal-blocks/7100104/
1 | 5 | 826-515 | Avago Technologies | HLMP-K150 | LED RED | LED | RS Components | http://uk.rs-online.com/web/p/visible-leds/0826515
1 | 5 | 213-2222 | TE Connectivity | CRG0603F470R | 470ohm | R2 | RS Components | http://uk.rs-online.com/web/p/surface-mount-fixed-resistors/2132222
1 | 5 | 739-0303 | Fairchild Semiconductor | MMBT3904 | Transistor NPN | Q1 | RS Components | http://uk.rs-online.com/web/p/bipolar-transistors/7390303/
1 | 5 | 721-7340 | Panasonic | ERJP03F1001V | 1Kohm | R1 | RS Components | http://uk.rs-online.com/web/p/surface-mount-fixed-resistors/7217340/
1 | 5 | 796-9344 | Taiwan Semiconductor | RS1D | Blocking Diode | D1 | RS Components | http://uk.rs-online.com/web/p/rectifier-schottky-diodes/7969344/
1 | 5 | 680-3595 | TE Connectivity | PE014005 | 5V Non latch relay | K1 | RS Components | http://uk.rs-online.com/web/p/non-latching-relays/6803593/
1 | 5 |  |  |  | 5*5cm Prototype Board |  | Itead Studio

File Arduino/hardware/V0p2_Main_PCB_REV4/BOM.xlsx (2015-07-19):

# of boards ttl |  |  |  |  |  |  | 5 | Green MEANS OK
Quantity per board | Total for this Batch | MOQ | Seller Stock No | Unit Price | Line Total | Manufacturer | Manufacturer Part. No. | Description | Legend | Supplier | Direct Link
1 | 5 | 5 | 714-2334 | 0.498 | 2.49 | FCI | 10103592-0001LF | Micro USB socket | USBPOWER | RS Components | http://uk.rs-online.com/web/p/micro-usb-connectors/7142334/
1 | 5 | 10 | 628-3661 | 0.244 | 1.22 | Microchip | TC1185-3.3VCT713 | 3.3V Regulator | U1 | RS Components | http://uk.rs-online.com/web/p/low-dropout-voltage-regulators/6283661
3 | 15 | 50 | 741-4434 | 0.103 | 1.54 | TDK | C1608X5R0J106M080AB | 10 uF | C1, C2, C13 | RS Components | http://uk.rs-online.com/web/p/ceramic-multilayer-capacitors/7414434
1 | 5 | 50 | 213-2581 | 0.013 | 0.07 | TE Connectivity | CRG0603F220K | 220Kohm | R1 | RS Components | http://uk.rs-online.com/web/p/surface-mount-fixed-resistors/2132581/
2 | 10 | 50 | 213-2367 | 0.008 | 0.08 | TE Connectivity | CRG0603F4K7 | 4.7Kohm | R4, R5, R2, R6, R8, R9, R12 | RS Components | http://uk.rs-online.com/web/p/surface-mount-fixed-resistors/2132367
1 | 5 | 50 | 213-2222 | 0.007 | 0.04 | TE Connectivity | CRG0603F470R | 470ohm | R7 | RS Components | http://uk.rs-online.com/web/p/surface-mount-fixed-resistors/2132222
5 | 25 | 25 | 264-4630 | 0.022 | 0.55 | Kemet | C0603C104K4RAC | 100nF | C7, C9, C10, C11, C12 | RS Components | http://uk.rs-online.com/web/p/ceramic-multilayer-capacitors/2644630
1 | 5 | 50 | 464-6391 | 0.006 | 0.03 | AVX | 06035A101JAT2A | 100pF | C4 | RS Components | http://uk.rs-online.com/web/p/ceramic-multilayer-capacitors/4646391
1 | 5 | 5 | 749-2059 | 0.54 | 2.70 | Murata | GRM31CR60G107ME39L | 100uF | C8 | RS Components | http://uk.rs-online.com/web/p/ceramic-multilayer-capacitors/7492059
1 | 5 | 5 | 667-6120 | 0.8 | 4.00 | EPSON TOYOCOM | MC-306, 32.768kHz, 20ppm, 6pF | Crystal | Q1 | RS Components | http://uk.rs-online.com/web/p/crystal-units/6676120
2 | 10 | 5 | 220-4260 | 0.48 | 4.80 | Phoenix Contact | MPT 0.5/ 2-2.54 | Screw Terminal 2-way | X1, X2 | RS Components | http://uk.rs-online.com/web/p/pcb-terminal-blocks/2204260
1 | 5 | 1 | 786-5554 | 2.91 | 14.55 | Sensirion | SHT21 | SHT21 | SHT21 | RS Components | http://uk.rs-online.com/web/p/temperature-humidity-sensors/7865554/
1 | 5 | 10 | 681-2537 | 0.231 | 1.16 | TE Connectivity | 826947-6 | FTDI 90 angle header | FTDI | RS Components | http://uk.rs-online.com/web/p/pcb-headers/6812537
1 | 5 | 10 | 674-2450 | 0.236 | 1.18 | ASSMANN WSW | A 28-LC/7-T | 28 pin IC Socket | IC1 | RS Components | http://uk.rs-online.com/web/p/dil-sockets/6742450
2 | 10 | 25 | 251-8086 | 0.054 | 0.54 | RS | W81102T3825RC | Jumper pin | JP1, JP2 | RS Components | http://uk.rs-online.com/web/p/pcb-headers/2518086
2 | 10 | 10 | 680-1461 | 0.103 | 1.03 | TE Connectivity | 1-881545-1 | Jumper cap | [fit to JP1, JP2] | RS Components | http://uk.rs-online.com/web/p/jumpers-shunts/6801461
1 | 5 | 5 | 826-515 | 0.348 | 1.74 | Avago Technologies | HLMP-K150 | LED RED | LED | RS Components | http://uk.rs-online.com/web/p/visible-leds/0826515
1 | 5 | 10 | 700-0776 | 0.319 | 1.59 | Vishay | TEPT4400 | 60° Visible Light Phototransistor | PHT | RS Components | http://uk.rs-online.com/web/p/phototransistors/7000776/
2 | 10 | 20 | 758-1991 | 0.11 | 1.10 | Alps | SKHHLQA010 | Learn | S1, S2 | RS Components | http://uk.rs-online.com/web/p/tactile-switches/7581991
1 | 5 | 1 | 263-3006 | 0.5 | 2.50 | Alps | RK09K1110A96 | Pot. Meter | R11 | RS Components | http://uk.rs-online.com/web/p/potentiometers/2633006
1 | 5 | 50 | 213-2266 | 0.006 | 0.03 | TE Connectivity | CRG0603F1K0 | 1Kohm | R10 | RS Components | http://uk.rs-online.com/web/p/surface-mount-fixed-resistors/2132266
1 | 5 | 3 | 119-2958 | 1.9 | 9.50 | Apem | 1415NC RED | Mode button on flying leads to BRB1, BRB2 | Mode | RS Components | http://uk.rs-online.com/web/p/push-button-switches/1192958
1 | 5 | 1 | 712-5320 | 0.006132 | 0.03 | RS | (1 reel of 100m for 7.30) | 84mm* of insulated semi-flexible antenna wire (~0.33sqmm). *Depends on PCB track length. | ANT | RS Components | http://uk.rs-online.com/web/p/hookup-equipment-wire/7125320
1 | 5 | 1 | 696-2260 | 2.26 | 11.30 | Atmel | ATMEGA328P-PU | ATmega328P-PU | IC1 | RS Components | http://uk.rs-online.com/web/p/microcontrollers/6962260
1 | 5 | 1 | RFM23-868-S1 | 3.22 | 16.10 | HopeRF | RFM23-868-S1 | RFM23B | RFM23 | ideetron.nl | http://www.hoperf.nl/RFM23B
1 | 5 | 10 |  | 1.875 | 9.38 | itead | assuming $30 for 10 boards | 5*5cm Prototype Board | MAIN Board
 |  |  |  | Total | 89.24
 |  |  |  | Each unit | 17.85

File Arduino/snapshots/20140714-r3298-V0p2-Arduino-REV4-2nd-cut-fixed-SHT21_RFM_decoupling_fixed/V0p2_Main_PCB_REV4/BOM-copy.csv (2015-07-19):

# of boards ttl |  |  |  | 5 | Green MEANS OK
Quantity per board | Need to order | Seller Stock No | Manufacturer | Manufacturer Part. No. | Description | Legend | Supplier | Direct Link
1 | 5 | 714-2334 | FCI | 10103592-0001LF | Micro USB socket | USBPOWER | RS Components | http://uk.rs-online.com/web/p/micro-usb-connectors/7142334/
1 | 5 | 628-3661 | Microchip | TC1185-3.3VCT713 | 3.3V Regulator | U1 | RS Components | http://uk.rs-online.com/web/p/low-dropout-voltage-regulators/6283661
3 | 15 | 741-4434 | TDK | C1608X5R0J106M080AB | 10 uF | C1, C2, C13 | RS Components | http://uk.rs-online.com/web/p/ceramic-multilayer-capacitors/7414434
1 | 5 | 213-2581 | TE Connectivity | CRG0603F220K | 220Kohm | R1 | RS Components | http://uk.rs-online.com/web/p/surface-mount-fixed-resistors/2132531
3 | 15 | 213-2418 | TE Connectivity | CRG0603F10K | 10 Kohm | R2, R4, R5 | RS Components | http://uk.rs-online.com/web/p/surface-mount-fixed-resistors/2132418
3 | 15 | 213-2367 | TE Connectivity | CRG0603F4K7 | 4.7Kohm | R6, R8, R9 | RS Components | http://uk.rs-online.com/web/p/surface-mount-fixed-resistors/2132367
1 | 5 | 213-2222 | TE Connectivity | CRG0603F470R | 470ohm | R7 | RS Components | http://uk.rs-online.com/web/p/surface-mount-fixed-resistors/2132222
5 | 25 | 264-4630 | Kemet | C0603C104K4RAC | 100nF | C7, C9, C10, C11, C12 | RS Components | http://uk.rs-online.com/web/p/ceramic-multilayer-capacitors/2644630
1 | 5 | 464-6391 | AVX | 06035A101JAT2A | 100pF | C4 | RS Components | http://uk.rs-online.com/web/p/ceramic-multilayer-capacitors/4646391
1 | 5 | 749-2059 | Murata | GRM31CR60G107ME39L | 100uF | C8 | RS Components | http://uk.rs-online.com/web/p/ceramic-multilayer-capacitors/7492059
1 | 5 | 667-6120 | EPSON TOYOCOM | MC-306, 32.768kHz, 20ppm, 6pF | Crystal | Q1 | RS Components | http://uk.rs-online.com/web/p/crystal-units/6676120
2 | 10 | 220-4260 | Phoenix Contact | MPT 0.5/ 2-2.54 | Screw Terminal 2-way | X1, X2 | RS Components | http://uk.rs-online.com/web/p/pcb-terminal-blocks/2204260
1 | 5 | 786-5554 | Sensirion | SHT21 | SHT21 | SHT21 | RS Components | http://uk.rs-online.com/web/p/temperature-humidity-sensors/7865554/
1 | 5 | 681-2537 | TE Connectivity | 826947-6 | FTDI 90 angle header | FTDI | RS Components | http://uk.rs-online.com/web/p/pcb-headers/6812537
1 | 5 | 674-2450 | ASSMANN WSW | A 28-LC/7-T | 28 pin IC Socket | IC1 | RS Components | http://uk.rs-online.com/web/p/dil-sockets/6742450
2 | 10 | 251-8086 | RS | W81102T3825RC | Jumper pin | JP1, JP2 | RS Components | http://uk.rs-online.com/web/p/pcb-headers/2518086
2 | 10 | 680-1461 | TE Connectivity | 1-881545-1 | Jumper cap | [fit to JP1, JP2] | RS Components | http://uk.rs-online.com/web/p/jumpers-shunts/6801461
1 | 5 | 826-515 | Avago Technologies | HLMP-K150 | LED RED | LED | RS Components | http://uk.rs-online.com/web/p/visible-leds/0826515
1 | 5 | 700-0776 | Vishay | TEPT4400 | 60° Visible Light Phototransistor | PHT | RS Components | http://uk.rs-online.com/web/p/phototransistors/7000776/
2 | 10 | 758-1991 | Alps | SKHHLQA010 | Learn | S1, S2 | RS Components | http://uk.rs-online.com/web/p/tactile-switches/7581991
1 | 5 | 263-3006 | Alps | RK09K1110A96 | Pot. Meter | R11 | RS Components | http://uk.rs-online.com/web/p/potentiometers/2633006
1 | 5 | 213-2266 | TE Connectivity | CRG0603F1K0 | 1Kohm | R10 | RS Components | http://uk.rs-online.com/web/p/surface-mount-fixed-resistors/2132266
1 | 5 | 119-2958 | Apem | 1415NC RED | Mode button | Mode | RS Components | http://uk.rs-online.com/web/p/push-button-switches/1192958
1 | 5 | 712-5320 |  |  | 84mm* of insulated semi-flexible antenna wire (~0.33sqmm). *Depends on PCB track length. | ANT |  | http://uk.rs-online.com/web/p/hookup-equipment-wire/7125320
1 | 5 | 696-2260 | Atmel | ATMEGA328P-PU | ATmega328P-PU | IC1 | RS Components | http://uk.rs-online.com/web/p/microcontrollers/6962260
1 | 5 | RFM23-868-S1 | HopeRF | RFM23-868-S1 | RFM23B | RFM23 | ideetron.nl | http://www.hoperf.nl/RFM23B
1 | 5 |  |  |  | 5*5cm Prototype Board | MAIN Board | Itead Studio
EXPERIMENTATION:
0 | 0 |  |  |  |  | R3 | NOT FITTED

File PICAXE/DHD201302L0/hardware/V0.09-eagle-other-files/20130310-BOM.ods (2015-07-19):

# of boards | 7
Quantity per board | Quantity Needed | Manually adjusted | Minimum Buy | Price each | Line total | Seller Stock No | Manufacturer Part. No. | Description | Supplier
1 | 7 | 7 | 1 | 1.4 | 1.4 | 705-1490 | 35RASMT4BHNTRX | Stereo jack | RS Components
1 | 7 | 7 | 5 | 0.322 | 1.61 | 714-2334 | 10103592-0001LF | Micro USB | RS Components
1 | 7 | 7 | 10 | 0.322 | 3.22 | 628-3661 | TC1185-3.3VCT713 | 3.3V Regulator | RS Components
1 | 7 | 7 | 1 | 4.25 | 4.25 | 732-7321 | DS1306E+ | DS1306 | RS Components
2 | 14 | 14 | 50 | 0.1 | 5 | 741-4434 | C1608X5R0J106M080AB | 10 uF | RS Components
1 | 7 | 7 | 50 | 0.018 | 0.9 | 213-2418 | CRG0603F10K | 10 Kohm | RS Components
1 | 7 | 7 | 50 | 0.012 | 0.6 | 213-2452 | CRG0603F22K | 22 kohm | RS Components
1 | 7 | 7 | 50 | 0.007 | 0.35 | 213-2367 | CRG0603F4K7 | 4.7Kohm | RS Components
1 | 7 | 7 | 5 | 0.282 | 1.41 | 700-7907 | SML-211UTT86 | SMD LED Red 630nm 18deg Clear 0805 | RS Components
3 | 21 | 21 | 25 | 0.02 | 0.5 | 264-4630 | C0603C104K4RAC | 100nF | RS Components
1 | 7 | 7 | 5 | 0.096 | 0.48 | 749-2059 | GRM31CR60G107ME39L | 100uF | RS Components
1 | 7 | 7 | 50 | 0.034 | 1.7 | 464-6391 | 06035A101JAT2A | 100pF | RS Components
7 | 49 | 49 | 50 | 0.012 | 0.6 | 213-2531 | CRG0603F100K | 100Kohm | RS Components
1 | 7 | 7 | 50 | 0.012 | 0.6 | 213-2222 | CRG0603F470R | 470ohm | RS Components
1 | 7 | 7 | 5 | 0.8 | 4 | 667-6120 | MC-306, 32.768kHz, 20ppm, 6pF | Crystal | RS Components
1 | 7 | 7 | 5 | 0.094 | 0.47 | 229-2548 | L-483GDT | LED | RS Components
1 | 7 | 7 | 5 | 0.19 | 0.95 | 710-0444 | 1776275-2 | Screw Terminal | RS Components
1 | 7 | 5 | 5 | 0.73 | 3.65 | 267-7416 | W35532TRC | PCB Sockets | RS Components
1 | 7 | 2 | 1 | 4.29 | 4.29 | 716-6936 | NEXC104Z3.5V10.5X5.5TRF | supercap | RS Components
1 | 7 | 7 | 1 | 1.79 | 1.79 | FH59P |  | push button | maplin | (ordered 2013/03/10)
1 | 7 | 7 | 1 | 2.2 | 2.2 | AXE015M2SM |  | PicAXE 18M2+ | techsupplies | (ordered 2013/03/10)
1 | 7 | 5 | 1 | 2.39 | 2.39 | ICO011 |  | DS18B20+ | techsupplies
1 | 7 | 7 | 1 | 0.24 | 0.24 | SEN002 |  | LDR | techsupplies
 |  | 2 | 1 | 9.99 | 9.99 | AXE027 |  | USB download cable | techsupplies
1 | 7 | 7 | 1 | 4.747 | 4.747 | RFM23-868-S1 | RFM23-868-S1 | RFM23B | TME | (ordered 2013/03/10)

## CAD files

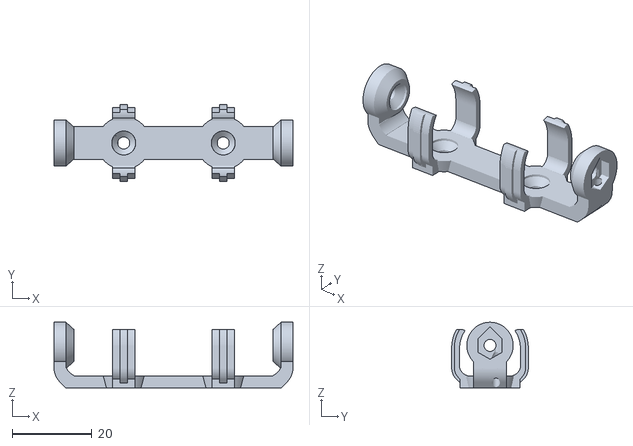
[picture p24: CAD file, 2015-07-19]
mechanics/box/roughs/AA_1_Battery_Holder.stl
59.8 x 19.2 x 16.4

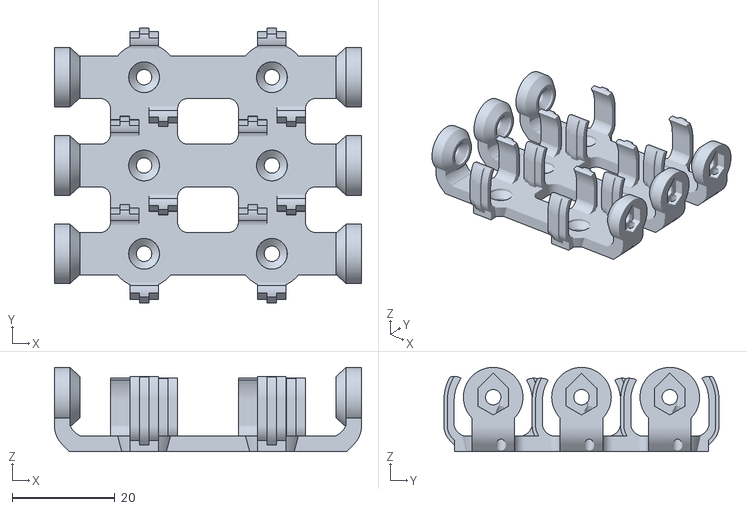
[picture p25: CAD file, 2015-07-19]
mechanics/box/roughs/AA_3_Battery_Holder.stl
59.8 x 53.6 x 16.4

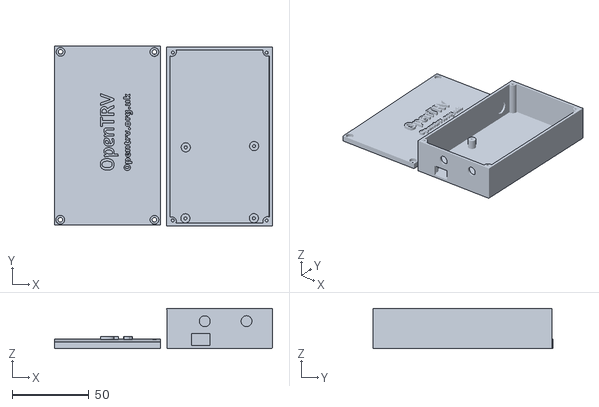
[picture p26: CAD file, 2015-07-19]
mechanics/box/roughs/Case 2.stl
142.2 x 117.6 x 26.4

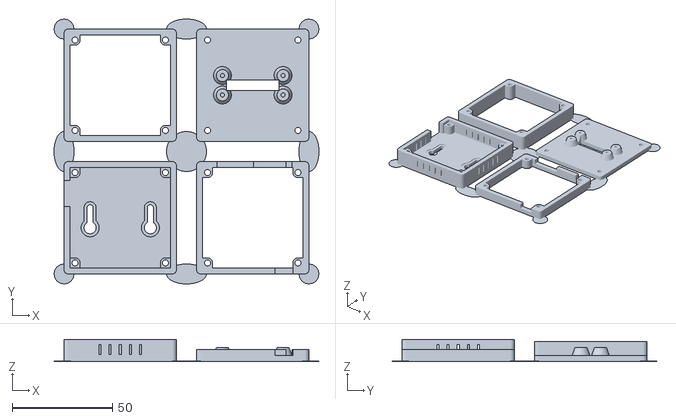
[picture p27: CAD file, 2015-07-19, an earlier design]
mechanics/box/V0p2_AVR_REV1_layered_box/20131208/box-v0_2r1.stl
132.0 x 132.0 x 11.0

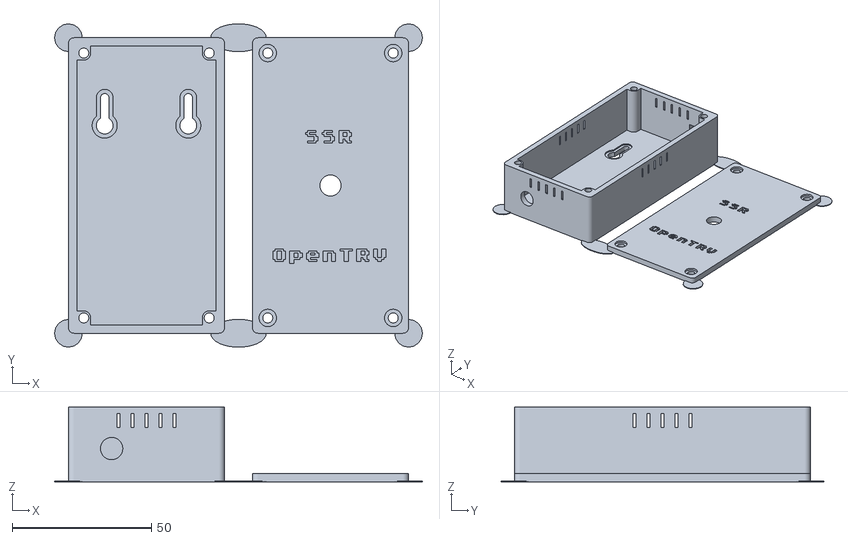
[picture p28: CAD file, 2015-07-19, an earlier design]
mechanics/box/V0p2_AVR_REV1_layered_box/20131215/box-SSR.stl
132.0 x 116.0 x 26.9

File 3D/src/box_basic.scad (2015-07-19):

/*
The OpenTRV project licenses this file to you
under the Apache Licence, Version 2.0 (the "Licence");
you may not use this file except in compliance
with the Licence. You may obtain a copy of the Licence at

http://www.apache.org/licenses/LICENSE-2.0

Unless required by applicable law or agreed to in writing,
software distributed under the Licence is distributed on an
"AS IS" BASIS, WITHOUT WARRANTIES OR CONDITIONS OF ANY
KIND, either express or implied. See the Licence for the
specific language governing permissions and limitations
under the Licence.

Author(s) / Copyright (s): Bruno Girin 2013
*/

include <settings.scad>;

box_total_width = pcb_width + 2 * box_wall_width;
box_cube_width = box_total_width - 2 * box_corner_radius;
box_total_length = pcb_length + 2 * box_wall_width;
box_cube_length = box_total_length - 2 * box_corner_radius;
mounting_hole_pcb_offset = pcb_mounting_hole_to_edge + pcb_mounting_hole_radius;
mounting_hole_box_offset = box_wall_width + mounting_hole_pcb_offset;

module box_mounting_hole() {
    translate([0, 0, -0.1])
    cylinder(r = pcb_mounting_hole_radius, h = box_layer_thickness + 0.2);
}

module box_mounting_holes() {
    union() {
        translate([
            -pcb_width / 2 + mounting_hole_pcb_offset,
            -pcb_length / 2 + mounting_hole_pcb_offset,
            0])
        box_mounting_hole();
        translate([
            +pcb_width / 2 - mounting_hole_pcb_offset,
            -pcb_length / 2 + mounting_hole_pcb_offset,
            0])
        box_mounting_hole();
        translate([
            +pcb_width / 2 - mounting_hole_pcb_offset,
            +pcb_length / 2 - mounting_hole_pcb_offset,
            0])
        box_mounting_hole();
        translate([
            -pcb_width / 2 + mounting_hole_pcb_offset,
            +pcb_length / 2 - mounting_hole_pcb_offset,
            0])
        box_mounting_hole();
    }
}

module box_mounting_hole_surround() {
    hull_cube_side = box_layer_thickness - box_corner_radius;
    surround_radius = pcb_mounting_hole_radius + pcb_mounting_hole_max_padding;
    hull() {
        cylinder(r = surround_radius,
            h = box_layer_thickness);
        translate([mounting_hole_pcb_offset, -surround_radius, 0])
            cube(size = [hull_cube_side, hull_cube_side, box_layer_thickness]);
        translate([-surround_radius, mounting_hole_pcb_offset, 0])
            cube(size = [hull_cube_side, hull_cube_side, box_layer_thickness]);
        translate([mounting_hole_pcb_offset, mounting_hole_pcb_offset, 0])
            cube(size = [hull_cube_side, hull_cube_side, box_layer_thickness]);
    }
}

module box_mounting_hole_surrounds() {
    union() {
        translate([
            -pcb_width / 2 + mounting_hole_pcb_offset,
            -pcb_length / 2 + mounting_hole_pcb_offset,
            0])
        rotate(a = 180, v = [0, 0, 1])
        box_mounting_hole_surround();
        translate([
            +pcb_width / 2 - mounting_hole_pcb_offset,
            -pcb_length / 2 + mounting_hole_pcb_offset,
            0])
        rotate(a = -90, v = [0, 0, 1])
        box_mounting_hole_surround();
        translate([
            +pcb_width / 2 - mounting_hole_pcb_offset,
            +pcb_length / 2 - mounting_hole_pcb_offset,
            0])
        box_mounting_hole_surround();
        translate([
            -pcb_width / 2 + mounting_hole_pcb_offset,
            +pcb_length / 2 - mounting_hole_pcb_offset,
            0])
        rotate(a = 90, v = [0, 0, 1])
        box_mounting_hole_surround();
    }
}

module box_base() {
    hull() {
        translate([-box_cube_width / 2, -box_cube_length / 2, 0])
        cylinder(r = box_corner_radius, h = box_layer_thickness);
        translate([+box_cube_width / 2, -box_cube_length / 2, 0])
        cylinder(r = box_corner_radius, h = box_layer_thickness);
        translate([+box_cube_width / 2, +box_cube_length / 2, 0])
        cylinder(r = box_corner_radius, h = box_layer_thickness);
        translate([-box_cube_width / 2, +box_cube_length / 2, 0])
        cylinder(r = box_corner_radius, h = box_layer_thickness);
    }
}

module pcb_hole() {
    translate([-pcb_width / 2, -pcb_length / 2, -0.1])
    cube(size = [pcb_width, pcb_length, box_layer_thickness + 0.2]);
}

module box_inside_tab(side, width, depth, offset) {
    if(side == TOP) {
        translate([offset - width / 2, pcb_length / 2 - depth, 0])
        cube(size = [width, depth, box_layer_thickness]);
    }
    if(side == BOTTOM) {
        translate([offset - width / 2, -pcb_length / 2 - 0.1, 0])
        cube(size = [width, depth + 0.1, box_layer_thickness]);
    }
    if(side == LEFT) {
        translate([-pcb_width / 2 - 0.1, offset - width / 2, 0])
        cube(size = [depth + 0.1, width, box_layer_thickness]);
    }
    if(side == RIGHT) {
        translate([pcb_width / 2 - depth, offset - width / 2, 0])
        cube(size = [depth + 0.1, width, box_layer_thickness]);
    }
}

module box_outside_hole(side, width, depth, offset) {
    if(side == TOP) {
        translate([offset - width / 2, box_total_length / 2 - depth, -0.1])
        cube(size = [width, depth, box_layer_thickness + 0.2]);
    }
    if(side == BOTTOM) {
        translate([offset - width / 2, -box_total_length / 2 - 0.1, -0.1])
        cube(size = [width, depth + 0.1, box_layer_thickness + 0.2]);
    }
    if(side == LEFT) {
        translate([-box_total_width / 2 - 0.1, offset - width / 2, -0.1])
        cube(size = [depth + 0.1, width, box_layer_thickness + 0.2]);
    }
    if(side == RIGHT) {
        translate([box_total_width / 2 - depth, offset - width / 2, -0.1])
        cube(size = [depth + 0.1, width, box_layer_thickness + 0.2]);
    }
}

module box_spacer_layer() {
    difference() {
        union() {
            difference() {
                box_base();
                pcb_hole();
            }
            box_mounting_hole_surrounds();
        }
        box_mounting_holes();
    }
}

module box_layer0() {
    difference() {
        box_base();
        box_mounting_holes();
    }
}

module box_layer1() {
    difference() {
        union() {
            box_spacer_layer();
            box_inside_tab(RIGHT, 7, 3, 9);
            box_inside_tab(RIGHT, 5, 3, -8);
            box_inside_tab(LEFT, 36, 2, 0);
            box_inside_tab(BOTTOM, 6, 3, 16);
            box_inside_tab(BOTTOM, 6, 3, -16);
            box_inside_tab(TOP, 28, 2, 0);
        }
        box_outside_hole(LEFT, 10, box_layer_thickness, -5.5);
    }
}

module box_layer2() {
    difference() {
        box_base();
        pcb_hole();
        box_outside_hole(LEFT, 10, box_layer_thickness + 0.1, -5.5);
    }
}

module box_layer3() {
    difference() {
        union() {
            box_spacer_layer();
            box_inside_tab(LEFT, 10 + 2 * box_layer_thickness, box_layer_thickness, -5.5);
            box_inside_tab(LEFT, 8, 20, -5.5);
        }
        box_outside_hole(LEFT, 10, box_layer_thickness, -5.5);
        box_outside_hole(LEFT, 6, box_layer_thickness + 18, -5.5);
    }
}

translate([0, 0, -15])
box_layer0();

translate([0, 0, -5])
box_layer1();

translate([0, 0, 5])
box_layer2();

translate([0, 0, 15])
box_layer3();

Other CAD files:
mechanics/box/V0p2_AVR_REV1_layered_box/20131208/fudge-factor-1/box-v0_2r1.stl
mechanics/box/V0p2_AVR_REV1_layered_box/20131211/box-v0_2r1.stl
mechanics/box/V0p2_AVR_REV1_layered_box/20131228/box-v0_2r1.stl
mechanics/box/V0p2_AVR_REV1_layered_box/20140127/box-v0_2r1.stl
mechanics/box/V0p2_AVR_REV1_layered_box/20131125/SSR_src/settings-SSR.scad
mechanics/box/V0p2_AVR_REV1_layered_box/20131125/SSR_src/box-SSR.scad

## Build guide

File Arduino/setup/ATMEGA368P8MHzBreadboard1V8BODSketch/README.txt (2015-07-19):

Add to IDE's boards.txt, eg /Applications/Arduino.app/Contents/Resources/Java/hardware/arduino/boards.txt.
(Or create as a boards.txt to put under hardware/2AAbreadboard in Arduino sketches directory, but will break compilation.)

8MHz internal RC clock / 8, so 1MHz effective (low fuse 0x62, default is not /8),
and with BOD set for 1.8V to allow operation with 2xAA rechargeables (extended fuse 0x06, default is 2.7V).

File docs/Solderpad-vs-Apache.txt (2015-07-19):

From: Damon Hart-Davis
Date: 16 April 2013 12:13:05 GMT+01:00
To: Closed list for developer discussions <opentrv-dev@lists.opentrv.org.uk>
Subject: Licensing

Hi,

I  just had a chat with Andrew Katz, a lawyer involved with the creation of the Solderpad (0.51) licence, a variant of Apache 2.0 that deals with some of the legal/IP issues beyond copyright and patents that Apache addresses:

http://solderpad.org/licenses/

From our discussion we determined that maybe the best thing to do to protect us from IP trolls and also to protect/comfort end users (commercial and non-commercial) is as follows:

All code (including the generation scripts for 3D shapes): Apache licence

Schematics: Solderpad licence (eg paste the text into the schematic like we already have with V0.09 and the Apache licence)

PCB: Solderpad licence by putting short text eg "Solderpad licence <URL>" linking to the licence text on the PCB legend

Generated 3D files (ie output of scripts): disclaim rights, eg add something to the output to the effect "we believe we retain no rights in this, but you may choose to regard this as licensed under Solderpad/Apache if you wish".

Any comments?

Rgds

Damon

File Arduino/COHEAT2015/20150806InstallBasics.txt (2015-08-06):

Installation Basics

Setting up the REV9/relay and FHT8V.

1) Put batteries in the FHT8V and note the house code that comes up after C1 and C2,
   eg for a display of C1 12 C2 34 then the house code is 12 34.

2) Fit the FHT8V to the rad once the motor has stopped whirring and A2 is shown if not already fitted.

3) Boot the REV9 on the CLI.  Hit send/return periodically to keep the CLI awake.

4) Press the FHT8V button and wait for the 0 to come up.

5) Enter the housecode immediately after the '>' CLI prompt comes up as H 12 34 for the above example.
   Entering the house codes like this should force the REV9 relay to restart the sync process.

6) The REV9 should show it starting to sync with the FHT8V and then about 2 minutes later show FHT SYNC FINAL.
   If the bleeper has not been disabled on the FHT8V then each of these should produce a bleep,
   confirming that everything is working.

7) The status messages (starting with =) on the REV9 should now show the valve position at 1%,
   and after about 2 minutes and an "FHT8V TX" the FHT8V should whirr a little and move to 1%.

8) If nothing is heard from the hub by the REV9 relay for a while
   (usually 30 minutes, less during initialisation)
   then the REV9 will show complaints about not hearing from the hub and moving to a safe valve position,
   the status messages should show 33%, and the FHT8V should move to 33% and show that on its display.

9) If the FHT8V stops hearing from the REV9 for an extended period it will move to (and show) 30%
   and shut down (not listen for any more radio comms) and need power cycling in conjunction with
   the REV9 to resync.

Note: the REV9 and FHT8V share a housecode/ID, so the REV9 is a proxy for the FHT8V.

REV2 hub to REV9 relay comms

1) At a REV2 send from the CLI a poll/command starting +CC1 ? eg:

    +CC1 ? 12 34 5 2 2 2

   to send to the REV9 (and thus FHT8V) with house code 12 34 in this case.
   This command also sets the valve position to 5%,
   and sets the LEDs to do green double-flashes for 60 seconds.

   See 20150803HubInteraction.txt for more details of the commands.

   You should also see a response from the REV9 with house code 12 34 such as:

    +CC1 * 12 34 25 0 98 62 1 1 1

   A REV9 relay will only respond to ? messages with its own house code in.

   See 20150803HubInteraction.txt for more details of the values.

REV9 relay to REV2 hub comms

1) Pressing a button on the REV9 should cause an alert to be sent to all listening REV2 hubs,
   seen as (from REV9 with housecode 12 34):

    +CC1 ! 12 34

2) That should be sent randomly about once every 2 minutes by the REV9 relay
   until the REV9 relay sees and responds to a poll from a REV2 hub.

Note: the initial (cut1) REV9 boards had the switch stuck in the on position.

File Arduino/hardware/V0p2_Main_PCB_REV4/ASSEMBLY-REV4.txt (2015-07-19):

A few points to note for PCB assembly.

 1A)**IF YOU ARE ASSEMBLING WITH ENCLOSURE** Mode button is on flying
    leads (~60mm) and needs to be fitted through lid (from front)
    before soldering up to the BRB1 and BRB2 connections.

 1B)**IF YOU ARE ___NOT___ ASSEMBLING WITH ENCLOSURE** Please solder
    60mm flying leads to board and strip and tin 4mm of free end of
    wires for both BRB1 and BRB2 connections. Please procure and
    supply Mode buttons and ship them loose to us with the boards.

 2) Top of LED should be 15mm (fifteen) above top surface of board
    so as to sit just behind hole in front panel.

 3) Top of LDR/Photo transistor should be 15mm (fifteen) above top surface of board
    so as to sit just behind hole in front panel

 4) Antenna wire should run straight, vertically out of box (if
    being enclosed), supporting its own weight (the wire is specified
    as single core in order to be self supporting).

 5) AVRs, once bootloaded and programmed, will conduct a Power On
    Self Test when power is applied to the board. The flashes of the
    LED will be in sequence: 1 flash, 2 flashes, 3 flashes, 4 flashes,
    5 flashes. At this point the LED will no longer flash obviously.
    Managing to reach 5 flashes in the sequence means that the POST
    succeeded and should be classed as a functional board. Bootloader
    and program will be supplied.

 6) For pot leg support holes milling can be replaced by slot drilling;
    leg is 2mm wide and mfr's diagram shows 2.1mm x 1.8mm slot.
    See: http://docs-europe.electrocomponents.com/webdocs/002a/0900766b8002ae35.pdf

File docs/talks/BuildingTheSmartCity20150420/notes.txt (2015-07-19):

OpenTRV - providing technology to revolutionise the way we heat our homes.

IoT / Cites / Stack

Here to save the planet: up to 8% of EU's entire carbon footprint on 500m radiators.

For that we need to be cheap (target GBP10/rad, payback in one winter).

For that we need to be open and interoperable.

For that we need IoT.

IoT Review

  * Lots of sensors (and some actuators)
    Business case: "If you can't measure, you can't manage..."

  * Internet often though not always involved
    OpenTRV's "home LAN" need not touch the Internet but the tech is the same when it does.

  * Lowest power things (smallest, cheapest) cannot directly support Internet sensibly
    Eg 22kB for IPv4 UDP on AVR.
    Which implies concentrators.
    Also militates against meshing.

  * Big pending issues: we're hoping to contribute over next 12 months!
    Standards/interop in data and comms.
    Security.

IoT in Cities

  * IoT Launchpad
    Buses (public transport generally), air, env key targets of IoT.
    Building health is another.
    Fine-grained monitoring such as temps and PMs may be hugely helpful.
    Preferably fit-and-forget, eg self-powered where mains not available.
    Cheap (and not worth nicking), secure, safe, reliable and accurate enough, open.

IoT Stack

  * 80% of IoT value and people in s/w side.
    Not everyone could or should wield at soldering iron.
    OpenTRV contribution is founders with experience all the way up the stack.
    Like being back in Personal Robots days with Z80A but with EEPROM, radio and nice IDE!

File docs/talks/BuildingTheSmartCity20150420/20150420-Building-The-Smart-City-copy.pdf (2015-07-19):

w | opentrv.org.uk
t | @opentrv
e | opentrv@opentrv.org.uk

# open TRV

# building the smart city

# Damon Hart-Davis

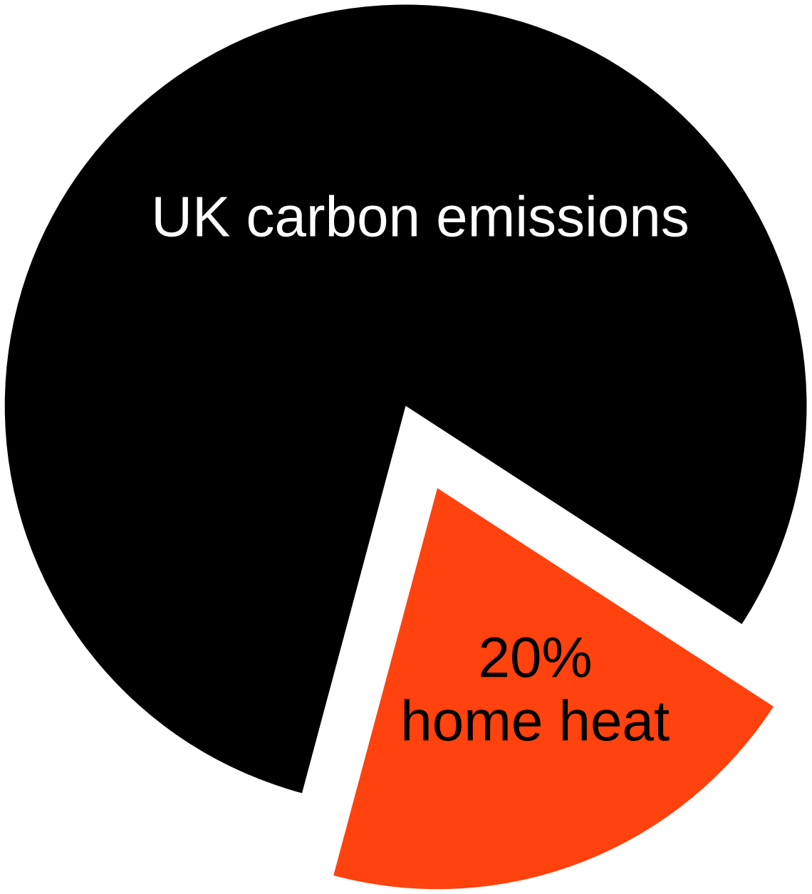
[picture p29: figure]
UK carbon emissions; 20% home heat

Problem: UK carbon emissions from domestic space heat 20%, gas bill £10bn/y, 50% wasted

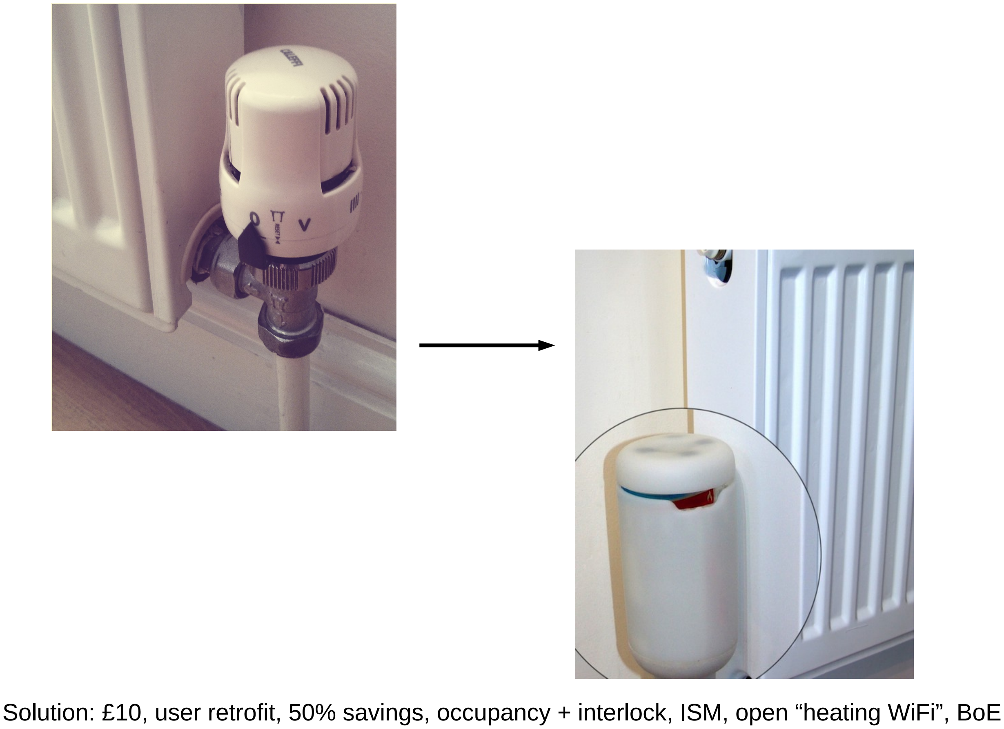
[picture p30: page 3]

Solution: £10, user retrofit, 50% savings, occupancy + interlock, ISM, open “heating WiFi”, BoE

# UK carbon emissions

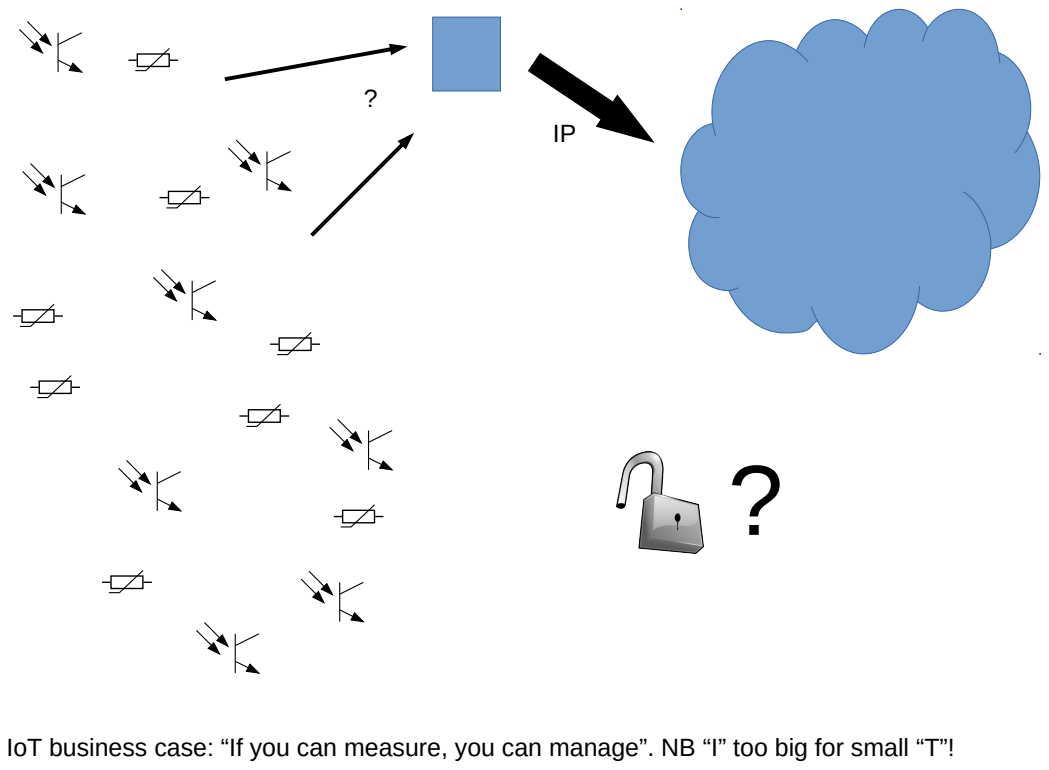
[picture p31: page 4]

IoT business case: “If you can measure, you can manage”. NB “I” too big for small “T”!

# UK carbon emissions

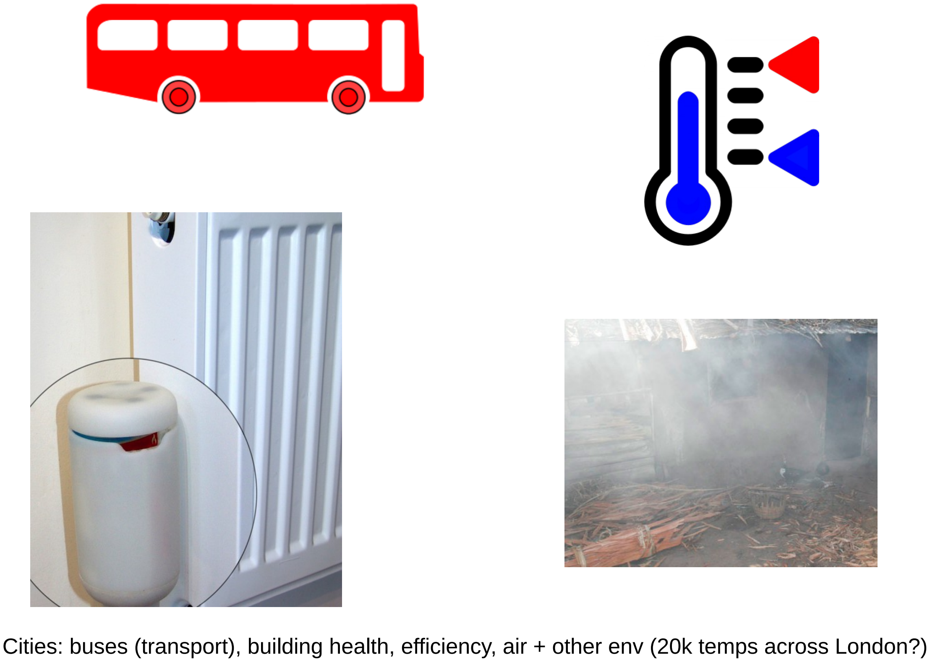
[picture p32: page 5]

Cities: buses (transport), building health, efficiency, air + other env (20k temps across London?)

# UK carbon emissions

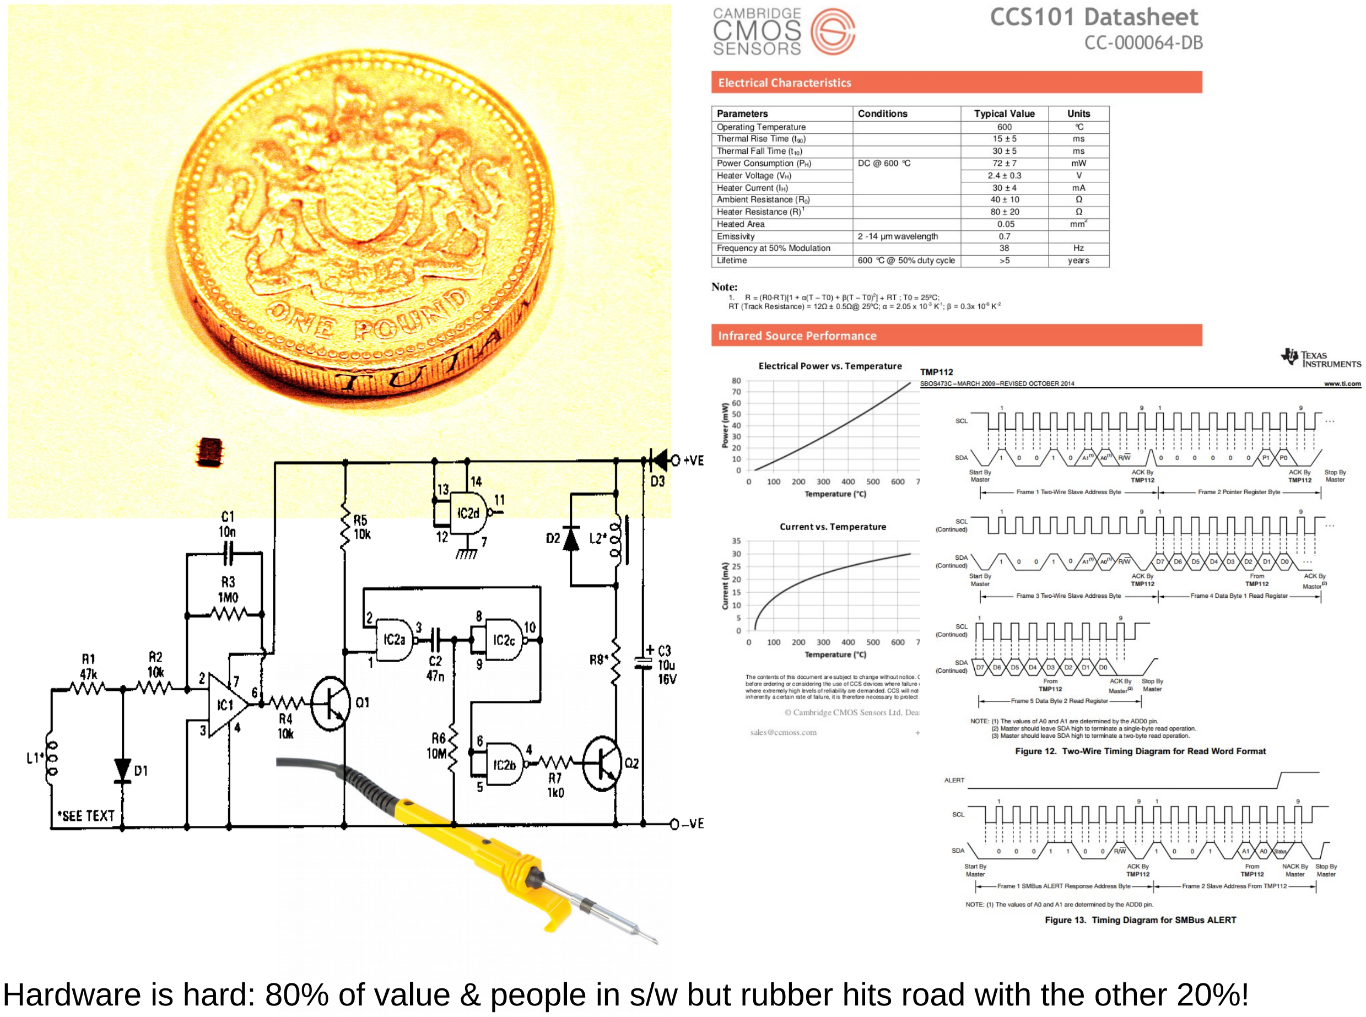
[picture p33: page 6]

Hardware is hard: 80% of value & people in s/w but rubber hits road with the other 20%!

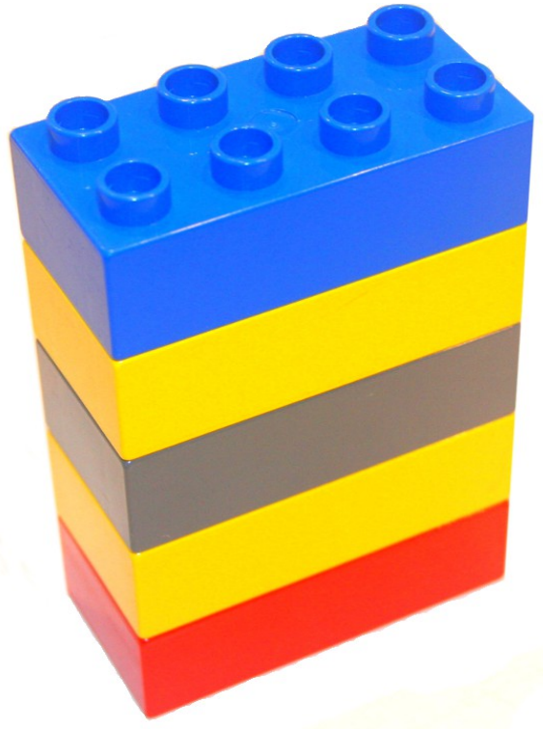
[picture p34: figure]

Horizonal: IoT technology; Innovate UK funding, new verticals in transport and building health

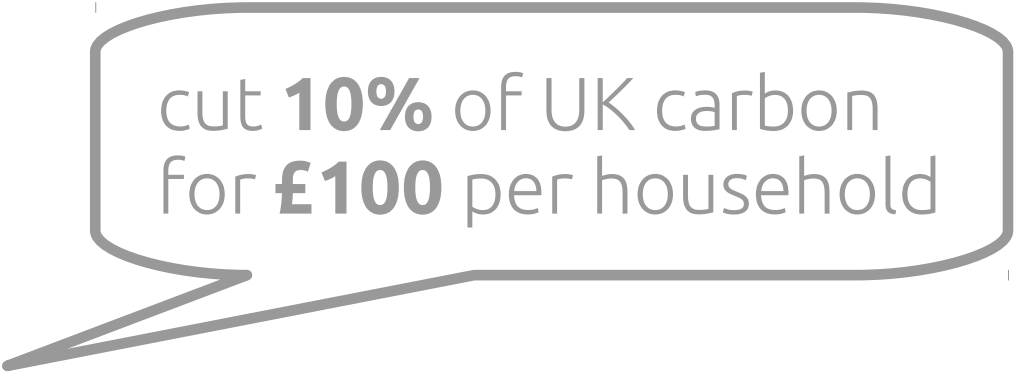
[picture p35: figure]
cut 10% of UK carbon for £100 per household

## Damon Hart-Davis

## @OpenTRV

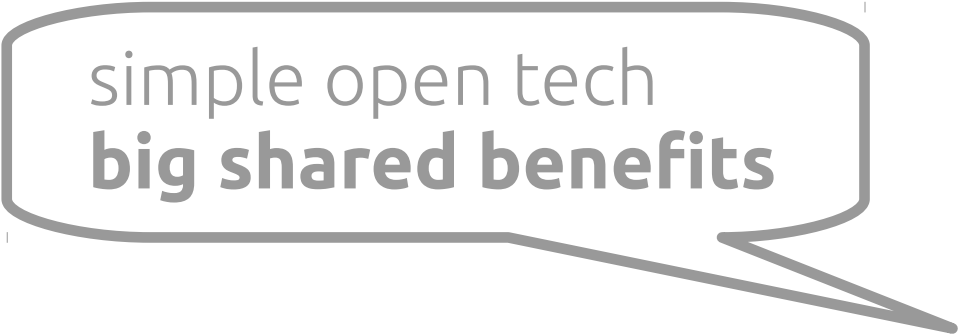
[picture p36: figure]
simple open tech big shared benefits

## open TRV

opentrv.org.uk

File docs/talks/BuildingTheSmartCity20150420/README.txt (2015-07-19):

http://www.eventbrite.co.uk/e/building-the-smart-city-an-iot-workshop-tickets-16034838634

Event Details

Join OpenSensors for a practical introduction to the systems, technologies and opportunities of the smarter city.

The Open Data Institute and Arup are hosting a smart cities event on 20th April which takes a forward-look at openness as the underlying driver for scaling smart cities. Following the morning's event, OpenSensors.io will be running an afternoon workshop as a practical introduction to the Internet of Things.

Through the course of the workshop, participants will:

    Gain a broad understanding of what the Internet of Things (IoT) actually is.

    Build an understanding of potential gains for cities showing examples of existing projects around parking, air quality monitoring. 

    Understand the core elements of the IoT stack; hardware, firmware, network connectivity, software, data.

Agenda

1400 - 1415 Registration/coffee

1415 - 1445 Maker time

1500 - 1530 Yodit Stanton, Co-Founder, CEO, OpenSensors.io - an Internet of Things technology startup passionate about building a connected world that puts people first. Yodit also runs Women in Data and has a history of machine learning and distributed computation through her career as a software dev in banking.

1530 - 1600 Ben Ward, Director, Love Hz - a network consultancy specialising in the Internet of Things and wireless sensor networks. A veteran of the UK Internet industry, Ben is also a resident of Oxford and a relentless innovator.

1600 - 1615 Coffee

1615 - 1645 Damon Hart-Davis & Mark Hill, Founders of OpenTRV - providing technology that seeks to revolutionise the way we heat our homes. Damon is a keen engineer, freelancing technology for over 30 years, leaving a string of successful startups in his wake, including Ixaris, with a turnover of ~GBP10m. With a wealth of experience from his years in the City designing and deliving complex systems, Mark now speaks regularly on innovation, collaboration and IoT - as well as founding a mobile software startup.

-

In this session we hope to provide an understanding of the new technologies and the wealth of opportunities promising to revolutionise both our environments and markets.

We look forward to seeing you there,

The OpenSensors Team

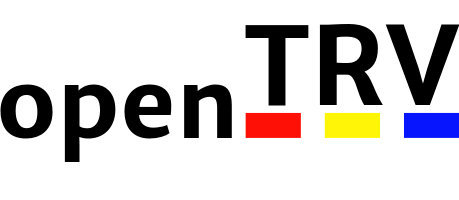
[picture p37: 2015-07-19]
docs/trials/Winter-2013-2014/installer-and-user-manuals/source/opentrv.200.png

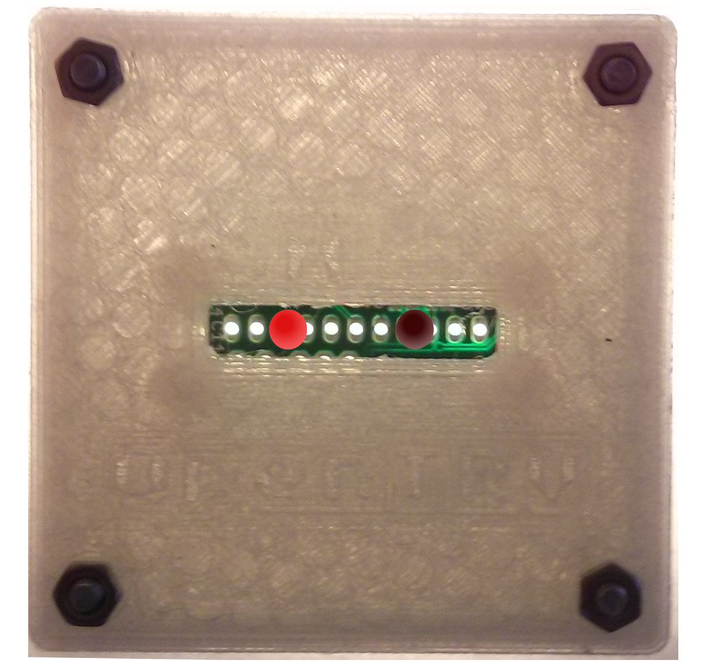
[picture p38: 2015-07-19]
docs/maker-fair-sandown-park/sources/backlit-box2.jpg

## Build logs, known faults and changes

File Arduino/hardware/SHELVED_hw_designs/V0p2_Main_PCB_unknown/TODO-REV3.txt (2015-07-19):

Outstanding issues with the PCB for rev 3.

TODO (initials/date for who noted the issue) - FIRST STEP IS ONLY ONE ALLOWED TO BE WORKED ON SO FAR

BELOW is Things to remember when sending off to fab:

BH20130916: for reflow go with ENIG finish - also important for TMP
DHD20130703: Send *ALL* generated Gerbers (eg including GML for milling)! 
BH20130916: TIP: normal I just zip up the gerbers and eagle files.. fab house did not have a problem with this last i send something off

DONE (w/ optional initials/date for who fixed the issue) - First 2 are done hardware wise.... need to code it thou
BH20131017: Correct date stamp
DHD20140203: TODO-123: Need 5V supply (via fat track from USB) for boiler control output.
DHD20131229: TODO-93: Add comfort/economy slider switch to REV2 schematic / board.
BG20131212: Push the USB connector away from the corner (to help with box design).
DHD20131229: TODO-88: Possibly move all cable entries to (same) side (to allow switches on the other)
DHD20140113: TODO-101: Widen supply tracks and add more decoupling caps.
DHD20140109: TODO-115: Move temp sensor near edge/vent and away from (pref also below) radio, reg and AVR heat sources.
DHD20131229: TODO-112: Remove one set of screw terminals to reduce cable exit space required.
DHD20131103: Provide sufficient clearance between connectors/terminals and board edges/posts.
BH20131027: check polarity on LED at ribbon cable connection at main board end
DHD201231021: Ensure 'do not throw in landfill' sign not covered up.
BH20130917: clean up legends etc.. make sure they are easy to read and don't overlap... DONE but please check
DHD20130930: ENSURE RFM23 WIRING CORRECT and works for RX also.
BH20130916: If possible find a runtime replacement option for TMP112 (eg look at simple http://www.hobbytronics.co.uk/ds18b20-arduino for trivial code, though with licence issues).
DHD20130913: Consider DS75LX as alternative to TMP112 for easier handling (note +/-2C and 13uA standby).
MS20130702: Since you have loads of spare IO, why not connect the RFM22B IRQ pin? (DHD: could make it an option.)  ..... its been at bottom of list.... would it bring any benefit????  Mike suggested 2 pins... i picked D9
BH20130917: Could we use D9 or D2-D4 for DS ?  BH20130917: Picked D2
BH20130917: ring of via throws DRC errors... quick fix is to remove them right before making gerbers   BH20130917: moved them just enough to not throw any DRC's
DHD20130901: Make TTH hole pads larger for easier hand soldering. BH20130917: done... screw terminals fitted for 5/3.3V 
DHD20130913: Add easy/extra GND reference point for logic analyser. BH20130917: done... next to boiler screw terminal
BH20130917: Prepped for DS chip
DHD20130916: Allow DS18B20 to be fitted in place of TMP112 when supply is 3.3V: detect sensor at runtime.
BH20130917: Replaced holes for power with screw terminal... holes should still be big enough for bare wires
DHD20130901: Double check BOM component list against schematic and keep in sorted order.
DHD20130720: USB connector still not mating to board correctly.
BH20131007: USB not symmetric... who can tell what needs to be moved and by how much?
DHD20130721: Specify Tech Supplies LDR in BOM for consistency with current kit.
DHD20130721: Only need pad(s) for RESET as only used during dev, and only occasionally.
DHD20130720: Extend TMP112 pads to make hand soldering easier.
DHD20130718: Add OpenTRV.org.uk (ie official URL) to board.
MS20130702: You have components on both sides. Not really a problem but it will complicate assembly if you want to do a run by pick and place (because one side needs to be glued down). You could argue that the through-hole stuff could go on the top and the SMT on the bottom, but in that case the RFM22 is still on the wrong side. BH20131007: All SMD stuff should now be on one side
DHD20130702: Fixes to USB connector layers (still asymmetry in GTS/GBS files).
MS20130702: Why not ground flood both sides?  DONE
DHD20130702: Fix C13 label and remove "100nF" text.
MS20130702: AREF should be decoupled.  DONE (100nF)
MS20130702: The jumper is underneath IC1 on the same side of the board, so will be inaccessible.  The solder blob will prevent the chip from being properly seated.  (Would like to eliminate entirely.) BH20131007 replced by 2 overlapping pads, the most easy way in my eyes
DHD20130702: Find some good way to eliminate SJ1 entirely.  See http://electronics.stackexchange.com/questions/23495/how-do-i-facilitate-keeping-multiple-grounds-i-e-agnd-dgnd-etc-separate BH20131007: replced by 2 overlapping pads, the most easy way in my eyes
MS20130702: What's with the AVR symbol? It looks kind of non-standard - is it some kind of weird Arduino version?  (BH hand-crafted but see http://www.cadsoftusa.com/downloads/libraries?language=en for future.)
MS20130702: A lot of the tracks could be thicker. If there is no need to make them thin then don't - you will get better board yield. I acknowledge that they have to be thin for connection to the TMP112, and where you pass between pads on the RFM22B (which I would have avoided). BH20131007: signal tracks are now 12 mil and supply 16 ant 86

Notes for antenna track thickness:
[10:54] DamonHD When you made the antenna track 50 ohm did you carefully choose a thickness? I've just slapped it up to 0.032 which looks vaguely right by eye. I could copy whatever you did on V0.09 board if it's critical.
[11:02] mikestir    the width is dependent on the board material and its thickness
[11:02] mikestir    http://www.eeweb.com/toolbox/microstrip-impedance
[11:02] mikestir    Er for FR4 is about 4 to 4.5

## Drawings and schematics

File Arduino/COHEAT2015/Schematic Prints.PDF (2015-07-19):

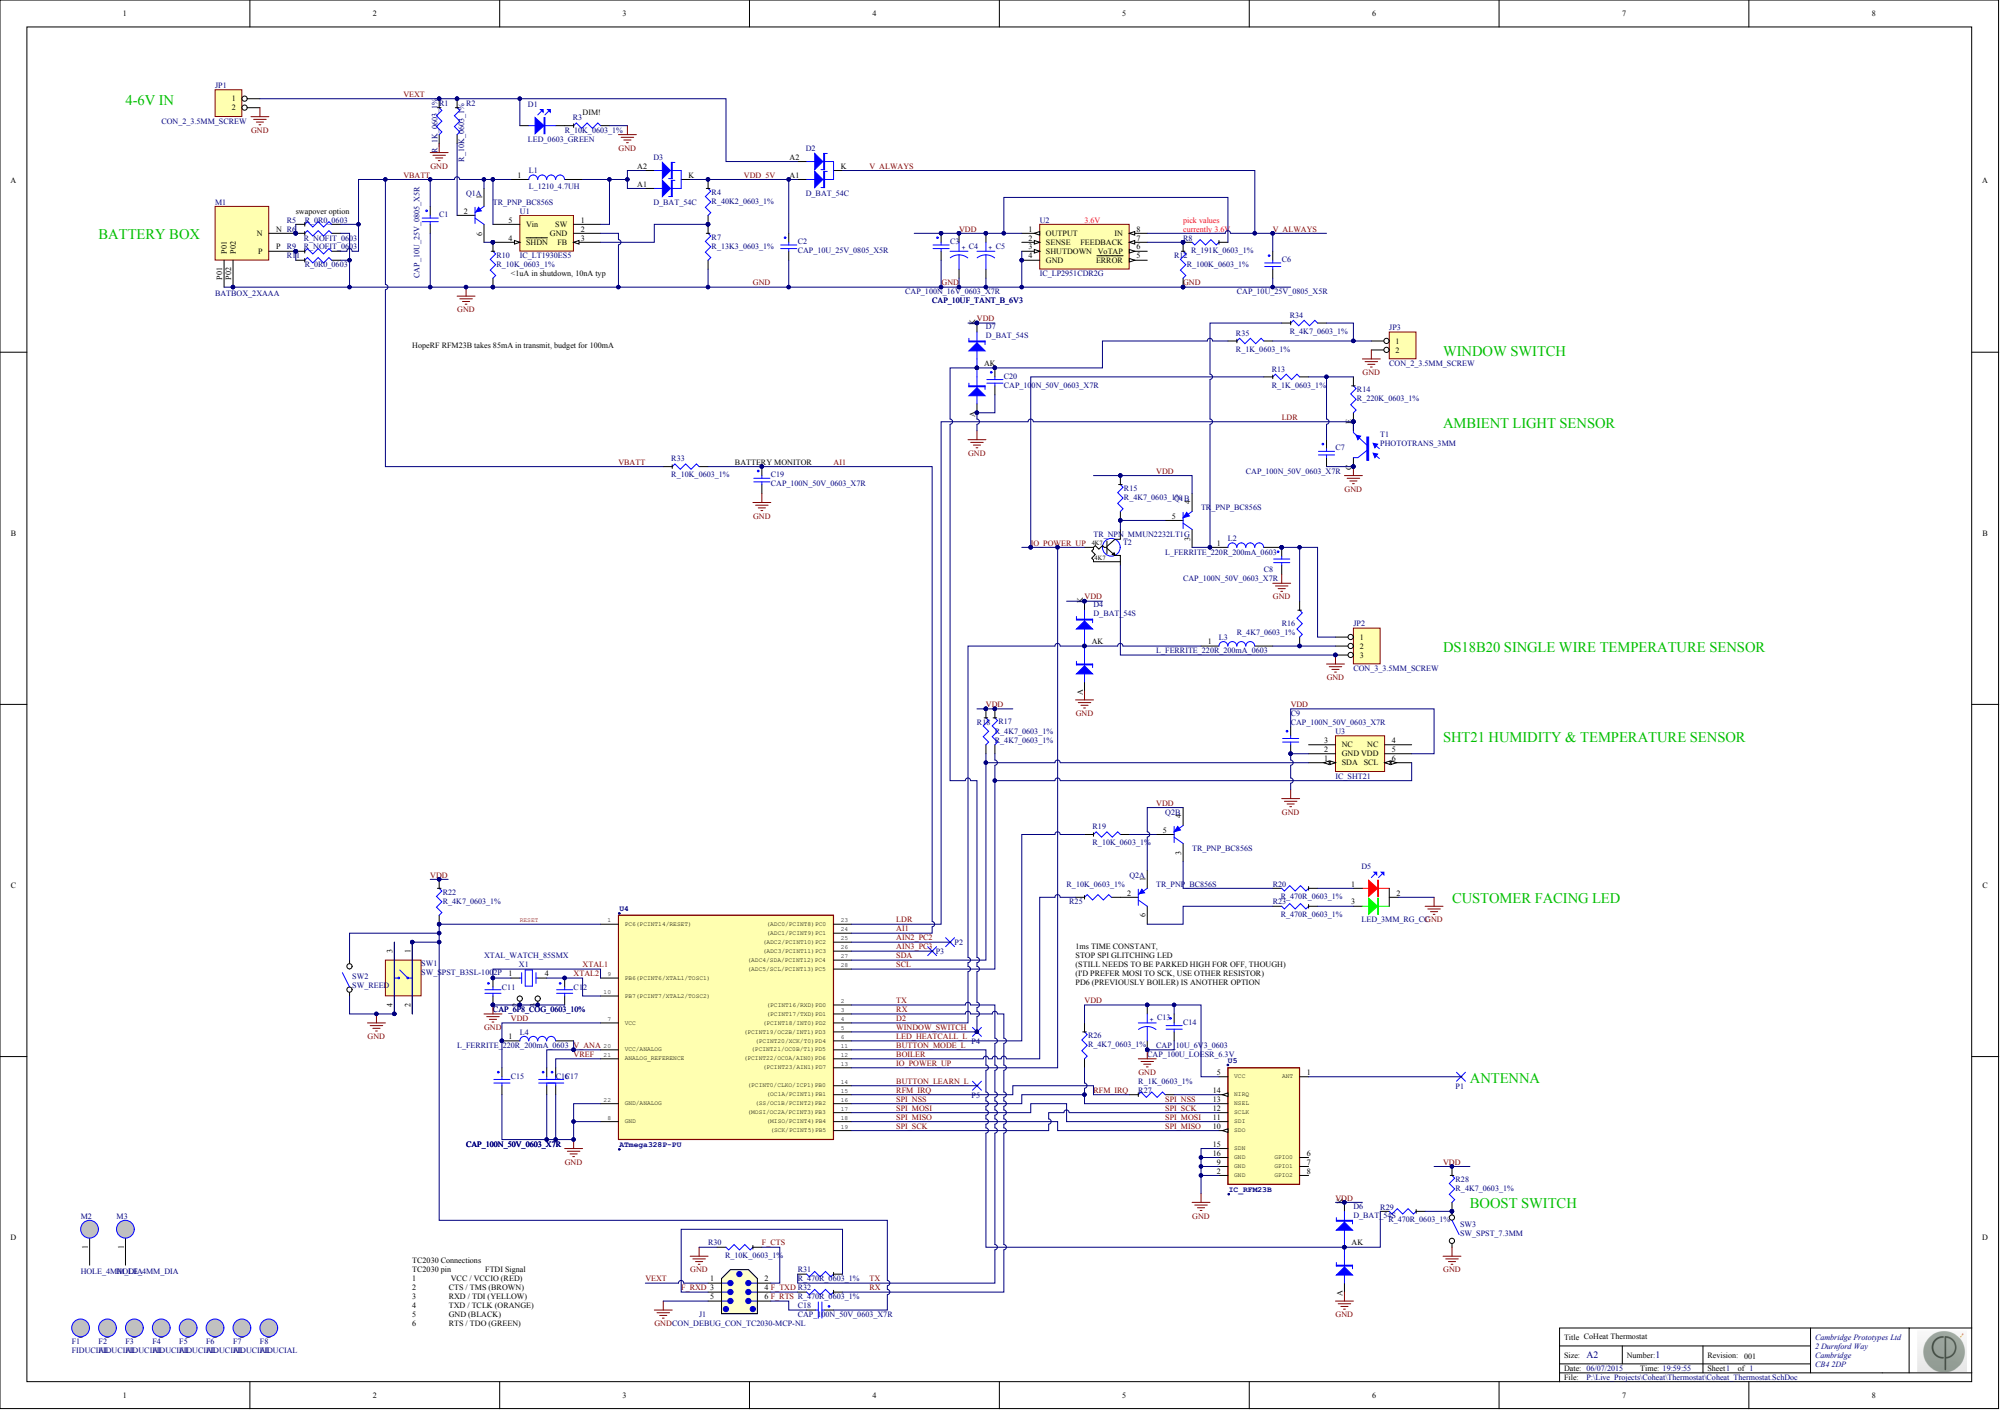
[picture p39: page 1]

HopeRF RFM23B takes 85mA in transmit, budget for 100mA

VDD | TR_PNP_BC856S | 1 L2

DS18B20 SINGLE WIRE TEMPERATURE SENSOR

1ms TIME CONSTANT,
STOP SPI GLITCHING LED
(STILL NEEDS TO BE PARKED HIGH FOR OFF, THOUGH)
(I'D PREFER MOSI TO SCK, USE OTHER RESISTOR)
PD6 (PREVIOUSLY BOILER) IS ANOTHER OPTION

1 L4 | | | WINDOW_SWITCH

LED_HEATCALL_L
P4 BUTTON_MODE_L

VREF | | ANALOG_REFERENCE 21 VCC/ANALOG 20 | BOILER

GND/ANALOG 22 | IO_POWER_UP

GND 8 | SPI_MOSI | | SPI_SCK | SCLK 12

SPI_MISO | | SPI_MOSI | SDI 11

CoHeat Thermostat Title | Cambridge Prototypes Ltd 2 Durnford Way Cambridge

Size: A2 | Number: 1 | Revision: 001
Date: 06/07/2015 Time: 19:59:55 | | Sheet 1 of | CB4 2DP 1

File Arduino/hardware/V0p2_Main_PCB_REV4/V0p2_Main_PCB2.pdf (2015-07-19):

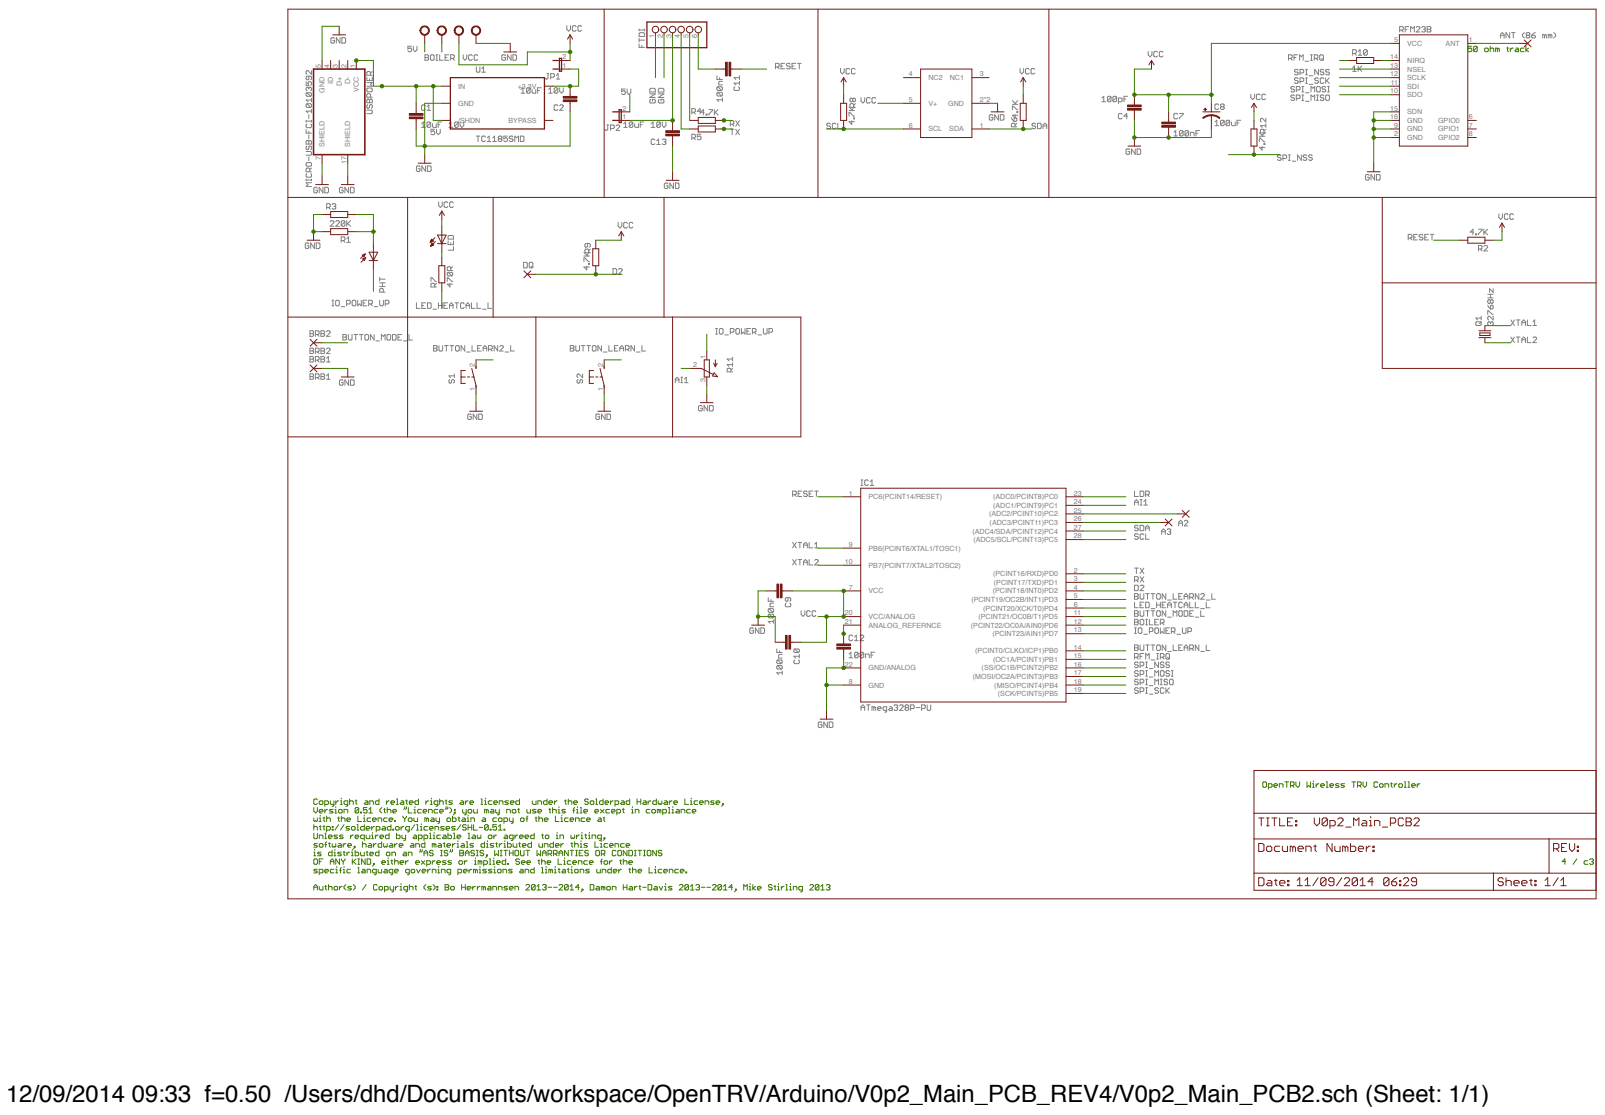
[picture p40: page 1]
GND; /SHDN; BYPASS; SCL 6; SDA; ANT; GND 2; GND 9; GND 16; GPIO0; GPIO1; GPIO2; NIRQ 14 NSEL 13 SCLK 12 SDI 11; SDN 15; SDO 10; VCC 5; (SCK/PCINT5)PB5; PB7(PCINT7/XTAL2/TOSC2) 10; PB6(PCINT6/XTAL1/TOSC1) 9; GND 8; VCC 7; GND/ANALOG 22; ANALOG_REFERNCE 21; VCC/ANALOG 20; (MISO/PCINT4)PB4; 18 (MOSI/OC2A/PCINT3)PB3; 17 (SS/OC1B/PCINT2)PB2; 16 (OC1A/PCINT1)PB1; 15 (PCINT0/CLKO/ICP1)PB0; (PCINT23/AIN1)PD7; 13 (PCINT22/OC0A/AIN0)PD6; 12 (PCINT21/OC0B/T1)PD5; 11 (PCINT20/XCK/T0)PD4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

VCC 1 D- 2 D+ 3 ID 4 GND 5 SHIELD 7 SHIELD 17

12/09/2014 09:33 f=0.50 /Users/dhd/Documents/workspace/OpenTRV/Arduino/V0p2_Main_PCB_REV4/V0p2_Main_PCB2.sch (Sheet: 1/1)

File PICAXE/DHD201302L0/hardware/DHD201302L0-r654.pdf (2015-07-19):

# DHD20130224 (r539+) Wireless TRV (& boiler) controller V0.09

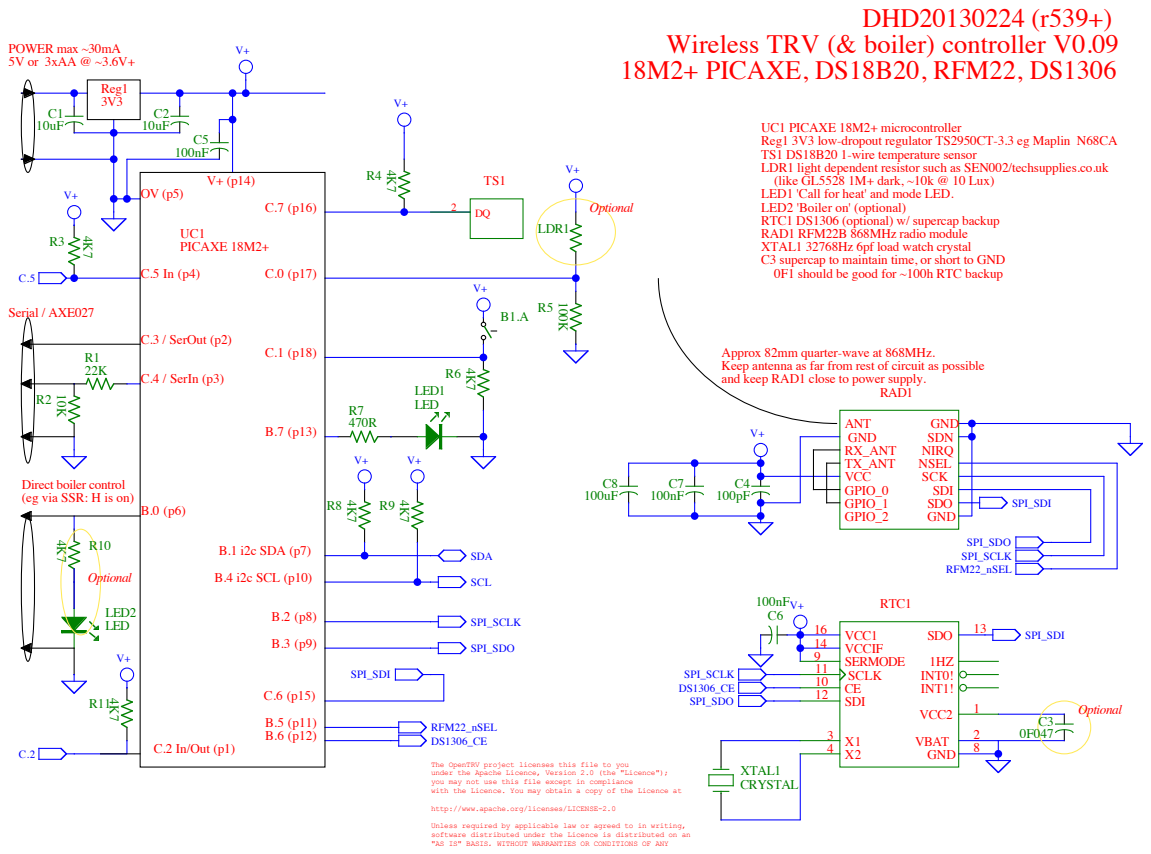
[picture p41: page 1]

UC1 PICAXE 18M2+ microcontroller
Reg1 3V3 low-dropout regulator TS2950CT-3.3 eg Maplin N68CA
TS1 DS18B20 1-wire temperature sensor
LDR1 light dependent resistor such as SEN002/techsupplies.co.uk
(like GL5528 1M+ dark, ~10k @ 10 Lux)
LED1 'Call for heat' and mode LED.
LED2 'Boiler on' (optional)
RTC1 DS1306 (optional) w/ supercap backup
RAD1 RFM22B 868MHz radio module
XTAL1 32768Hz 6pf load watch crystal
C3 supercap to maintain time, or short to GND
0F1 should be good for ~100h RTC backup

Approx 82mm quarter-wave at 868MHz.
Keep antenna as far from rest of circuit as possible
and keep RAD1 close to power supply.

Direct boiler control
(eg via SSR: H is on)

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

http://www.apache.org/licenses/LICENSE-2.0

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

Author(s): Damon Hart-Davis 2013

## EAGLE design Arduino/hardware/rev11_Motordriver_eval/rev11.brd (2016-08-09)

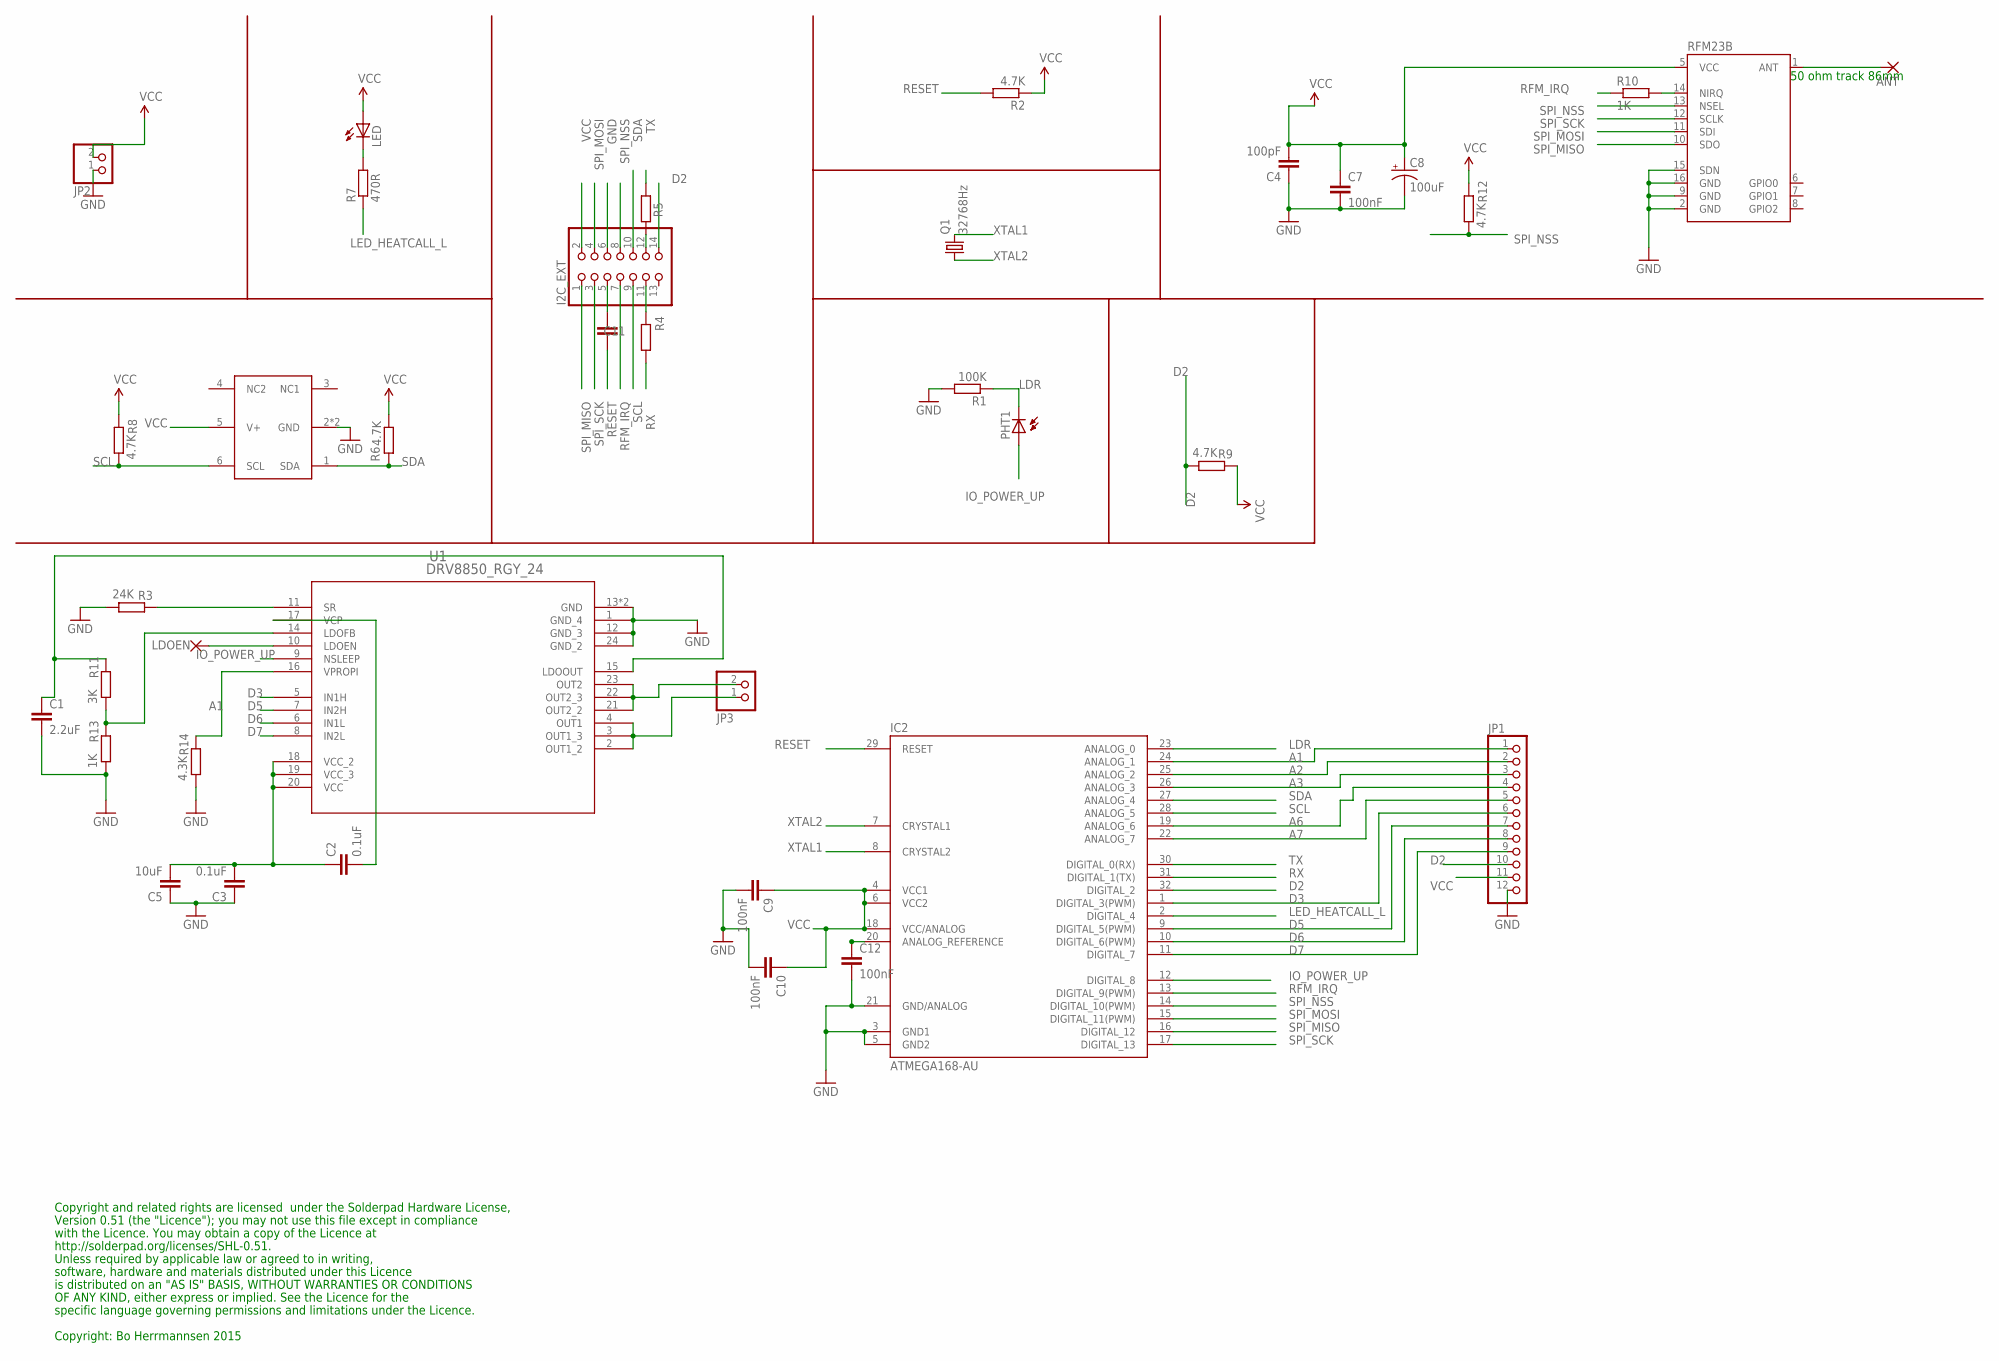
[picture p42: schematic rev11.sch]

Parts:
ANT: SMD2; SMD1,27-2,54
C1: 2.2uF; C0603
C2, C3: 0.1uF; C0603
C4: 100pF; C0603
C5: 10uF; C0603
C7, C9, C10, C11, C12: 100nF; C0603
C8: 100uF; EIA3216
I2C_EXT: PINHD-2X7; 2X07
IC2: ATMEGA168-AU; TQFP32-08
JP1: PINHD-1X12; 1X12
JP2, JP3: PINHD-1X2; 1X02
LDOEN: WIREPAD2,15/1,0; 2,15/1,0
LED: LEDCHIPLED_0603; CHIPLED_0603
PHT1: BPX65
Q1: 32768Hz; MC-306
R1: 100K; R0603
R2, R4, R5, R6, R8, R9, R12: 4.7K; R0603
R3: 24K; R0603
R7: 470R; R0603
R10, R13: 1K; R0603
R11: 3K; R0603
R14: 4.3K; R0603
RFM23B: RFM23B; RFM23-XXX-S1
U1: DRV8850_RGY_24; RGY_24
U$4: SHT21

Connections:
A1: IC2.24 (ANALOG_1), JP1.1, R14.2, U1.16 (VPROPI)
A2: IC2.25 (ANALOG_2), JP1.2
A3: IC2.26 (ANALOG_3), JP1.3
A6: IC2.19 (ANALOG_6), JP1.4
A7: IC2.22 (ANALOG_7), JP1.5
D2: I2C_EXT.14, IC2.32 (DIGITAL_2), JP1.10, R9.1
D3: IC2.1 (DIGITAL_3(PWM)), JP1.6, U1.5 (IN1H)
D5: IC2.9 (DIGITAL_5(PWM)), JP1.7, U1.7 (IN2H)
D6: IC2.10 (DIGITAL_6(PWM)), JP1.8, U1.6 (IN1L)
D7: IC2.11 (DIGITAL_7), JP1.9, U1.8 (IN2L)
GND: C1.2, C3.1, C4.1, C5.1, C7.2, C8.C (-), C9.2, C10.2, C12.2, I2C_EXT.6, IC2.3 (GND1), IC2.5 (GND2), IC2.21 (GND/ANALOG), JP1.12, JP2.1, R1.2, R3.1, R13.1, R14.1, RFM23B.2 (GND), RFM23B.9 (GND), RFM23B.15 (SDN), RFM23B.16 (GND), U1.1 (GND_4), U1.12 (GND_3), U1.13 (GND), U1.24 (GND_2), U1.25 (GND), U$4.2 (GND), U$4.P$1 (GND)
IO_POWER_UP: IC2.12 (DIGITAL_8), PHT1.A, U1.9 (NSLEEP)
LDR: IC2.23 (ANALOG_0), PHT1.K (C), R1.1
LED_HEATCALL_L: IC2.2 (DIGITAL_4), R7.1
unnamed: C11.2, I2C_EXT.5
unnamed: I2C_EXT.12, R5.2
unnamed: I2C_EXT.11, R4.2
unnamed: JP3.1, U1.2 (OUT1_2), U1.3 (OUT1_3), U1.4 (OUT1)
unnamed: C12.1, IC2.20 (ANALOG_REFERENCE)
unnamed: R10.2, RFM23B.14 (NIRQ)
unnamed: JP3.2, U1.21 (OUT2_2), U1.22 (OUT2_3), U1.23 (OUT2)
unnamed: R3.2, U1.11 (SR)
unnamed: LED.C, R7.2
unnamed: R11.1, R13.2, U1.14 (LDOFB)
unnamed: C1.1, R11.2, U1.15 (LDOOUT)
unnamed: LDOEN.1, U1.10 (LDOEN)
unnamed: C2.2, U1.17 (VCP)
unnamed: ANT.1, RFM23B.1 (ANT)
RESET: C11.1, IC2.29 (RESET), R2.2
RFM_IRQ: I2C_EXT.7, IC2.13 (DIGITAL_9(PWM)), R10.1
RX: IC2.31 (DIGITAL_1(TX)), R4.1
SCL: I2C_EXT.9, IC2.28 (ANALOG_5), R8.1, U$4.6 (SCL)
SDA: I2C_EXT.10, IC2.27 (ANALOG_4), R6.2, U$4.1 (SDA)
SPI_MISO: I2C_EXT.1, IC2.16 (DIGITAL_12), RFM23B.10 (SDO)
SPI_MOSI: I2C_EXT.4, IC2.15 (DIGITAL_11(PWM)), RFM23B.11 (SDI)
SPI_NSS: I2C_EXT.8, IC2.14 (DIGITAL_10(PWM)), R12.1, RFM23B.13 (NSEL)
SPI_SCK: I2C_EXT.3, IC2.17 (DIGITAL_13), RFM23B.12 (SCLK)
TX: IC2.30 (DIGITAL_0(RX)), R5.1
VCC: C2.1, C3.2, C4.2, C5.2, C7.1, C8.A (+), C9.1, C10.1, I2C_EXT.2, IC2.4 (VCC1), IC2.6 (VCC2), IC2.18 (VCC/ANALOG), JP1.11, JP2.2, LED.A, R2.1, R6.1, R8.2, R9.2, R12.2, RFM23B.5 (VCC), U1.18 (VCC_2), U1.19 (VCC_3), U1.20 (VCC), U$4.5 (V+)
XTAL1: IC2.8 (CRYSTAL2), Q1.4 (2)
XTAL2: IC2.7 (CRYSTAL1), Q1.1

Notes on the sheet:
Copyright and related rights are licensed under the Solderpad Hardware License,
Version 0.51 (the "Licence"); you may not use this file except in compliance
with the Licence. You may obtain a copy of the Licence at
http://solderpad.org/licenses/SHL-0.51.
Unless required by applicable law or agreed to in writing,
software, hardware and materials distributed under this Licence
is distributed on an "AS IS" BASIS, WITHOUT WARRANTIES OR CONDITIONS
OF ANY KIND, either express or implied. See the Licence for the
specific language governing permissions and limitations under the Licence.
50 ohm track 86mm
Copyright: Bo Herrmannsen 2015

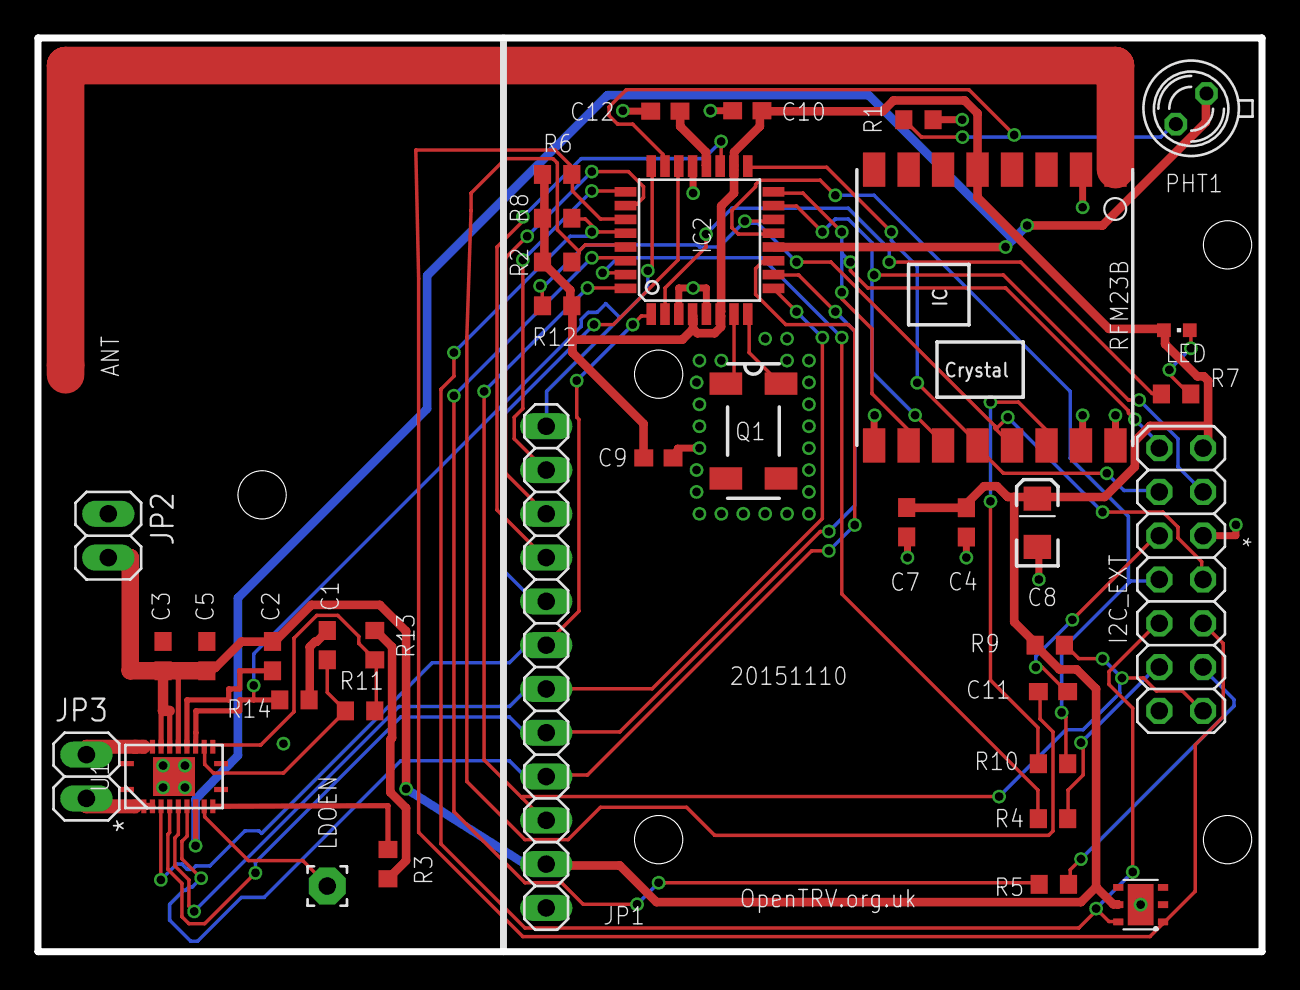
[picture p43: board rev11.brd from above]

Board: 2 copper layers, 71.0 x 53.0 mm, 40 parts (0 on the bottom side), 41 nets.

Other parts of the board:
U$1: OSHW_10X200_NOTEXT
U$2: TONNE

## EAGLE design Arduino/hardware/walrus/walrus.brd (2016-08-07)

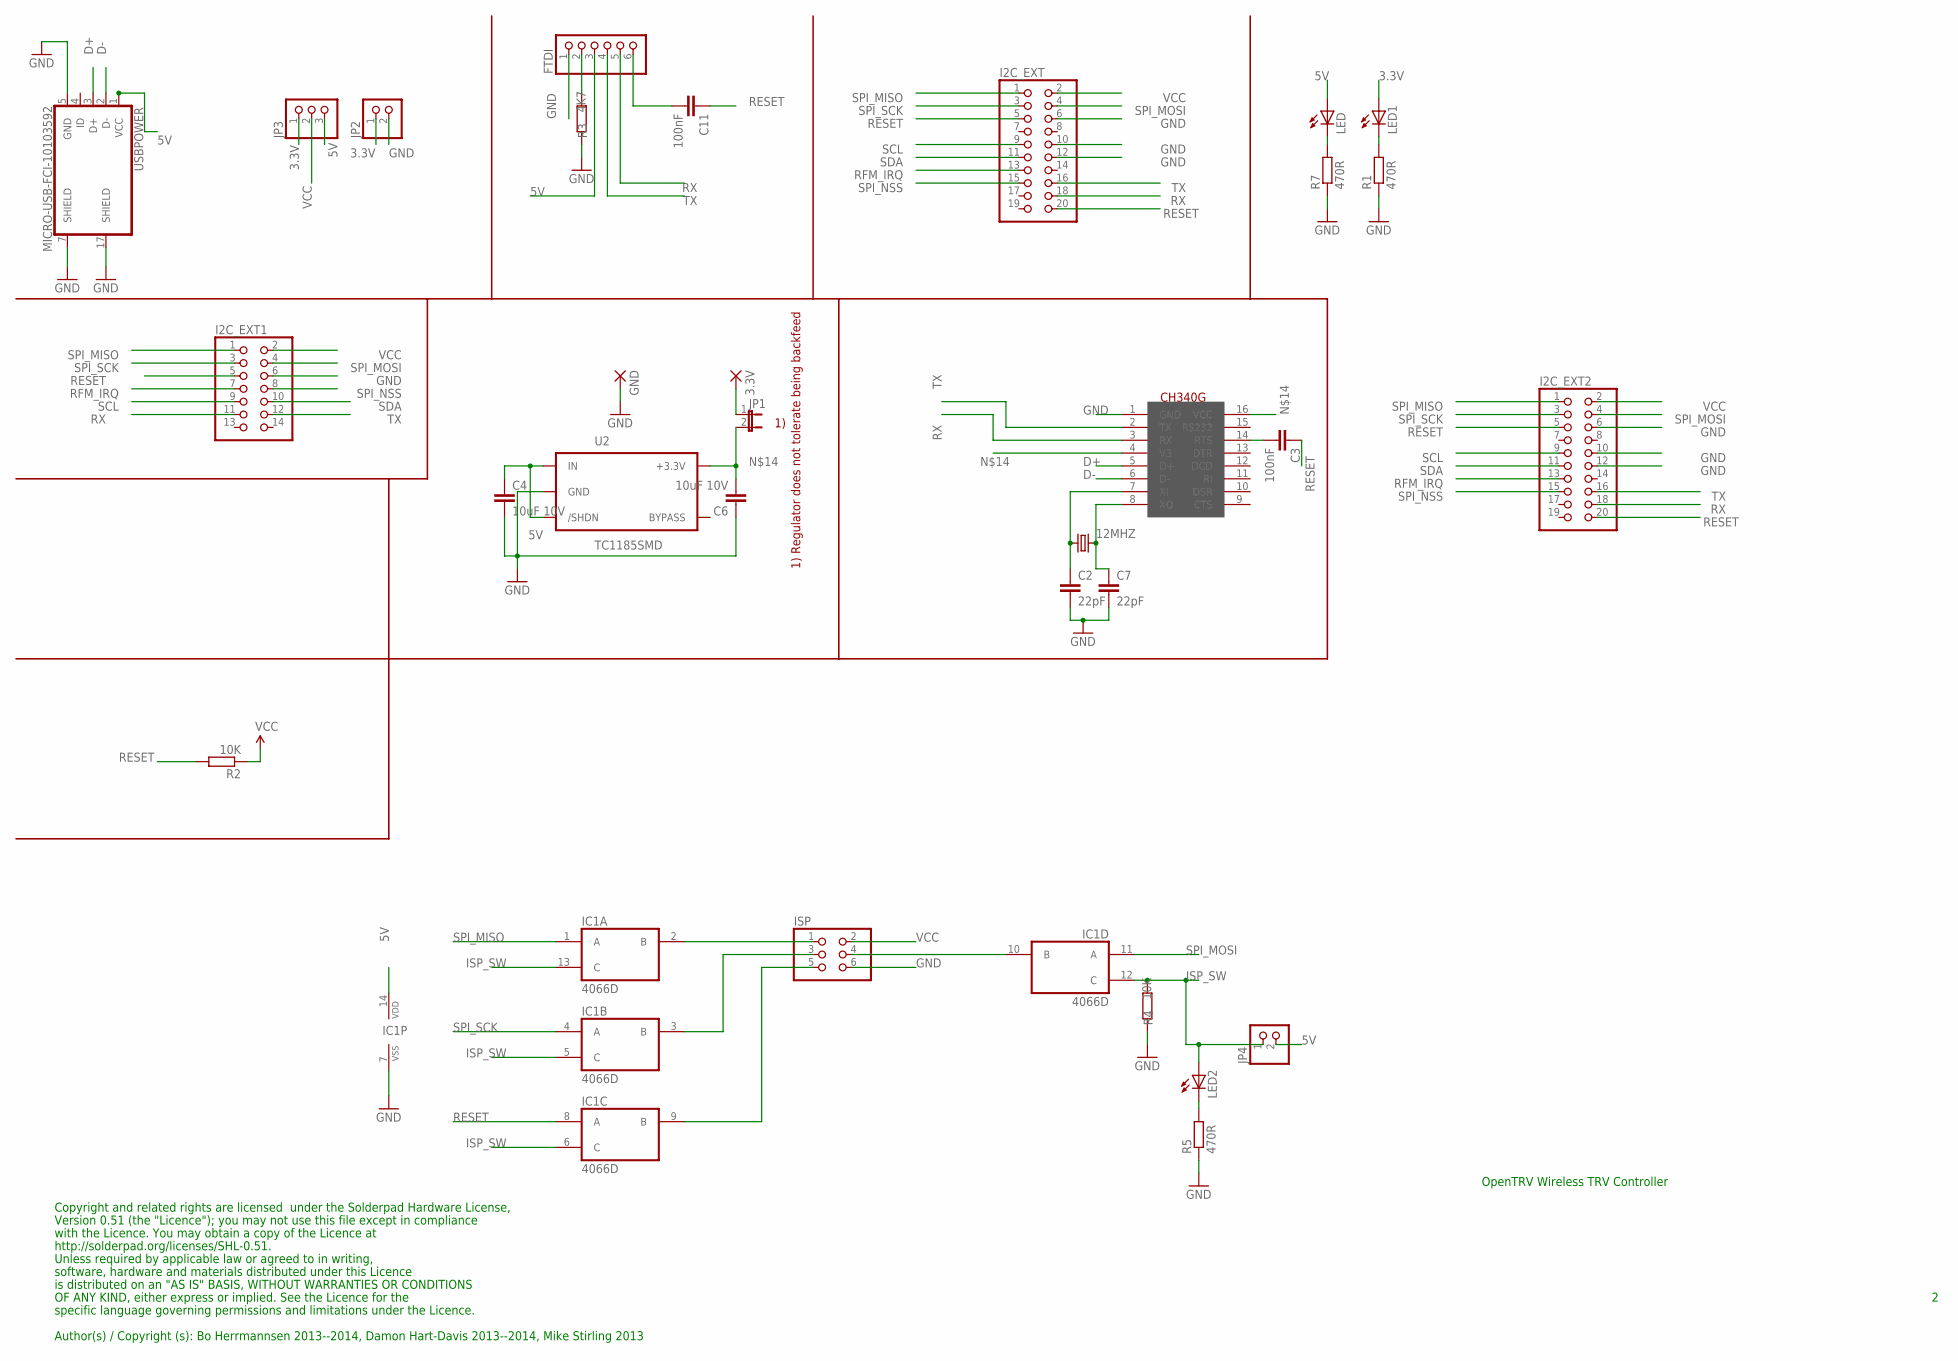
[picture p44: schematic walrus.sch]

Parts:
3.3V: 3,81/1,4
12MHZ: CRYSTALHC18U-V; HC18U-V
C2, C7: 22pF; C0603
C3, C11: 100nF; 0603-CAP
C4, C6: 10uF 10V; 0603-CAP
FTDI: PINHD-1X6/90; 1X06/90
GND: 3,81/1,4
I2C_EXT, I2C_EXT2: PINHD-2X10; 2X10
I2C_EXT1: PINHD-2X7; 2X07
IC1: 4066D; SO14
ISP: PINHD-2X3; 2X03
JP1: JP1E; JP1
JP2, JP4: PINHD-1X2; 1X02
JP3: PINHD-1X3; 1X03
LED, LED1, LED2: LEDCHIP-LED0603; CHIP-LED0603
R1, R5, R7: 470R; R0603
R2, R4: 10K; R0603
R3: 4K7; R0603
U2: TC1185SMD; TC1185
U$3: CH340G; SOIC16
USBPOWER: MICRO-USB-FCI-10103592

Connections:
3.3V: 3.3V.1, JP1.1, JP2.1, JP3.1, LED1.A
5V: C4.1, FTDI.3, IC1.14 (VDD), JP3.3, JP4.2, LED.A, U2.1 (IN), U2.3 (/SHDN), USBPOWER.1 (VCC)
D+: U$3.5 (D+), USBPOWER.3 (D+)
D-: U$3.6 (D-), USBPOWER.2 (D-)
GND: C2.2, C4.2, C6.1, C7.2, FTDI.1, GND.1, I2C_EXT.6, I2C_EXT.10, I2C_EXT.12, I2C_EXT1.6, I2C_EXT2.6, I2C_EXT2.10, I2C_EXT2.12, IC1.7 (VSS), ISP.6, JP2.2, R1.1, R3.1, R4.1, R5.1, R7.1, U2.2 (GND), U$3.1 (GND), USBPOWER.5 (GND), USBPOWER.7 (SHIELD), USBPOWER.17 (SHIELD)
ISP_SW: IC1.5 (C), IC1.6 (C), IC1.12 (C), IC1.13 (C), JP4.1, LED2.A, R4.2
unnamed: C11.2, FTDI.6
unnamed: C3.2, U$3.14 (RTS)
unnamed: FTDI.2, R3.2
unnamed: IC1.2 (B), ISP.1
unnamed: LED1.C, R1.2
unnamed: 12MHZ.1, C2.1, U$3.7 (XI)
unnamed: IC1.3 (B), ISP.3
unnamed: LED.C, R7.2
unnamed: C6.2, JP1.2, U2.5 (+3.3V), U$3.4 (V3), U$3.16 (VCC)
unnamed: 12MHZ.2, C7.1, U$3.8 (XO)
unnamed: IC1.9 (B), ISP.5
unnamed: IC1.10 (B), ISP.4
unnamed: LED2.C, R5.2
RESET: C3.1, C11.1, I2C_EXT.5, I2C_EXT.20, I2C_EXT1.5, I2C_EXT2.5, I2C_EXT2.20, IC1.8 (A), R2.2
RFM_IRQ: I2C_EXT.13, I2C_EXT1.7, I2C_EXT2.13
RX: FTDI.5, I2C_EXT.18, I2C_EXT1.11, I2C_EXT2.18, U$3.3 (RX)
SCL: I2C_EXT.9, I2C_EXT1.9, I2C_EXT2.9
SDA: I2C_EXT.11, I2C_EXT1.10, I2C_EXT2.11
SPI_MISO: I2C_EXT.1, I2C_EXT1.1, I2C_EXT2.1, IC1.1 (A)
SPI_MOSI: I2C_EXT.4, I2C_EXT1.4, I2C_EXT2.4, IC1.11 (A)
SPI_NSS: I2C_EXT.15, I2C_EXT1.8, I2C_EXT2.15
SPI_SCK: I2C_EXT.3, I2C_EXT1.3, I2C_EXT2.3, IC1.4 (A)
TX: FTDI.4, I2C_EXT.16, I2C_EXT1.12, I2C_EXT2.16, U$3.2 (TX)
VCC: I2C_EXT.2, I2C_EXT1.2, I2C_EXT2.2, ISP.2, JP3.2, R2.1

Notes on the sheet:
Copyright and related rights are licensed under the Solderpad Hardware License,
Version 0.51 (the "Licence"); you may not use this file except in compliance
with the Licence. You may obtain a copy of the Licence at
http://solderpad.org/licenses/SHL-0.51.
Unless required by applicable law or agreed to in writing,
software, hardware and materials distributed under this Licence
is distributed on an "AS IS" BASIS, WITHOUT WARRANTIES OR CONDITIONS
Author(s) / Copyright (s): Bo Herrmannsen 2013--2014, Damon Hart-Davis 2013--2014, Mike Stirling 2013
OpenTRV Wireless TRV Controller
OF ANY KIND, either express or implied. See the Licence for the
specific language governing permissions and limitations under the Licence.
1) Regulator does not tolerate being backfeed

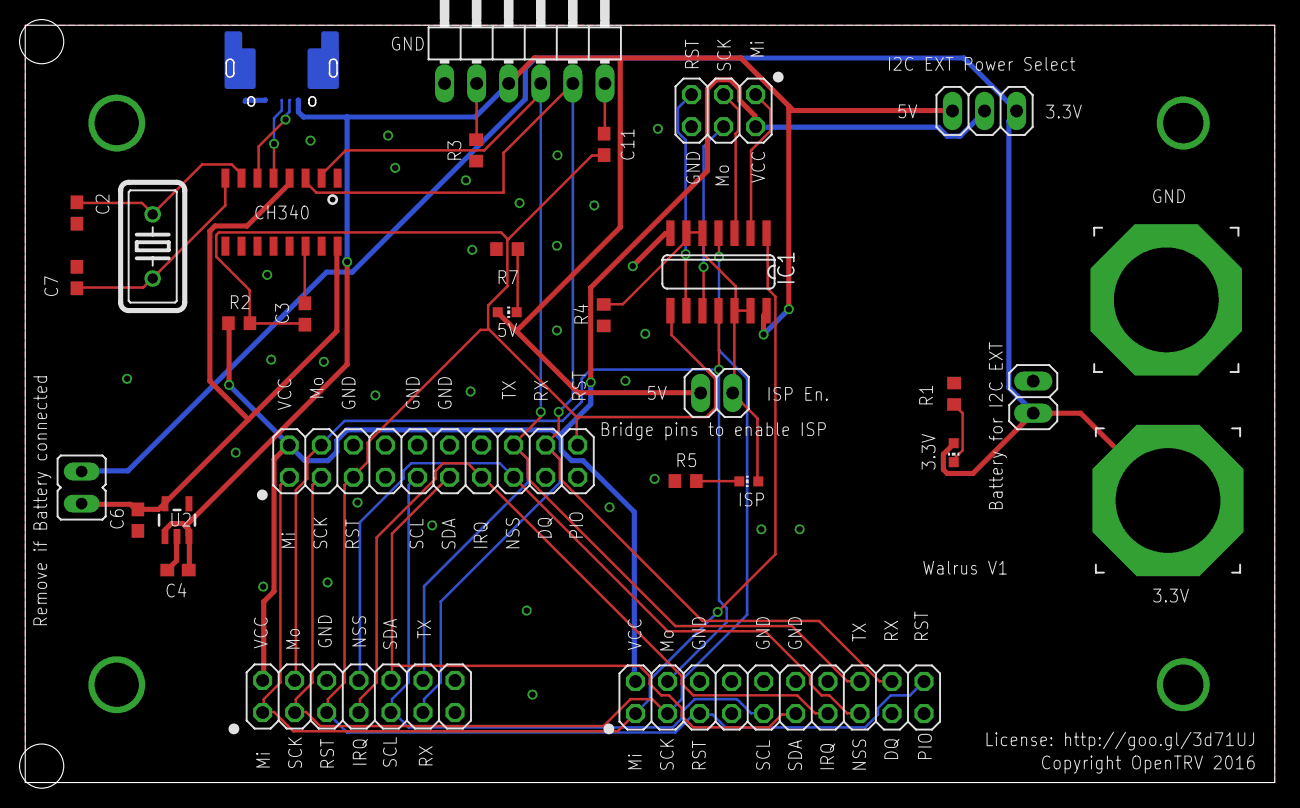
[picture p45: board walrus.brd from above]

Board: 2 copper layers, 99.0 x 60.0 mm, 31 parts (1 on the bottom side), 30 nets.

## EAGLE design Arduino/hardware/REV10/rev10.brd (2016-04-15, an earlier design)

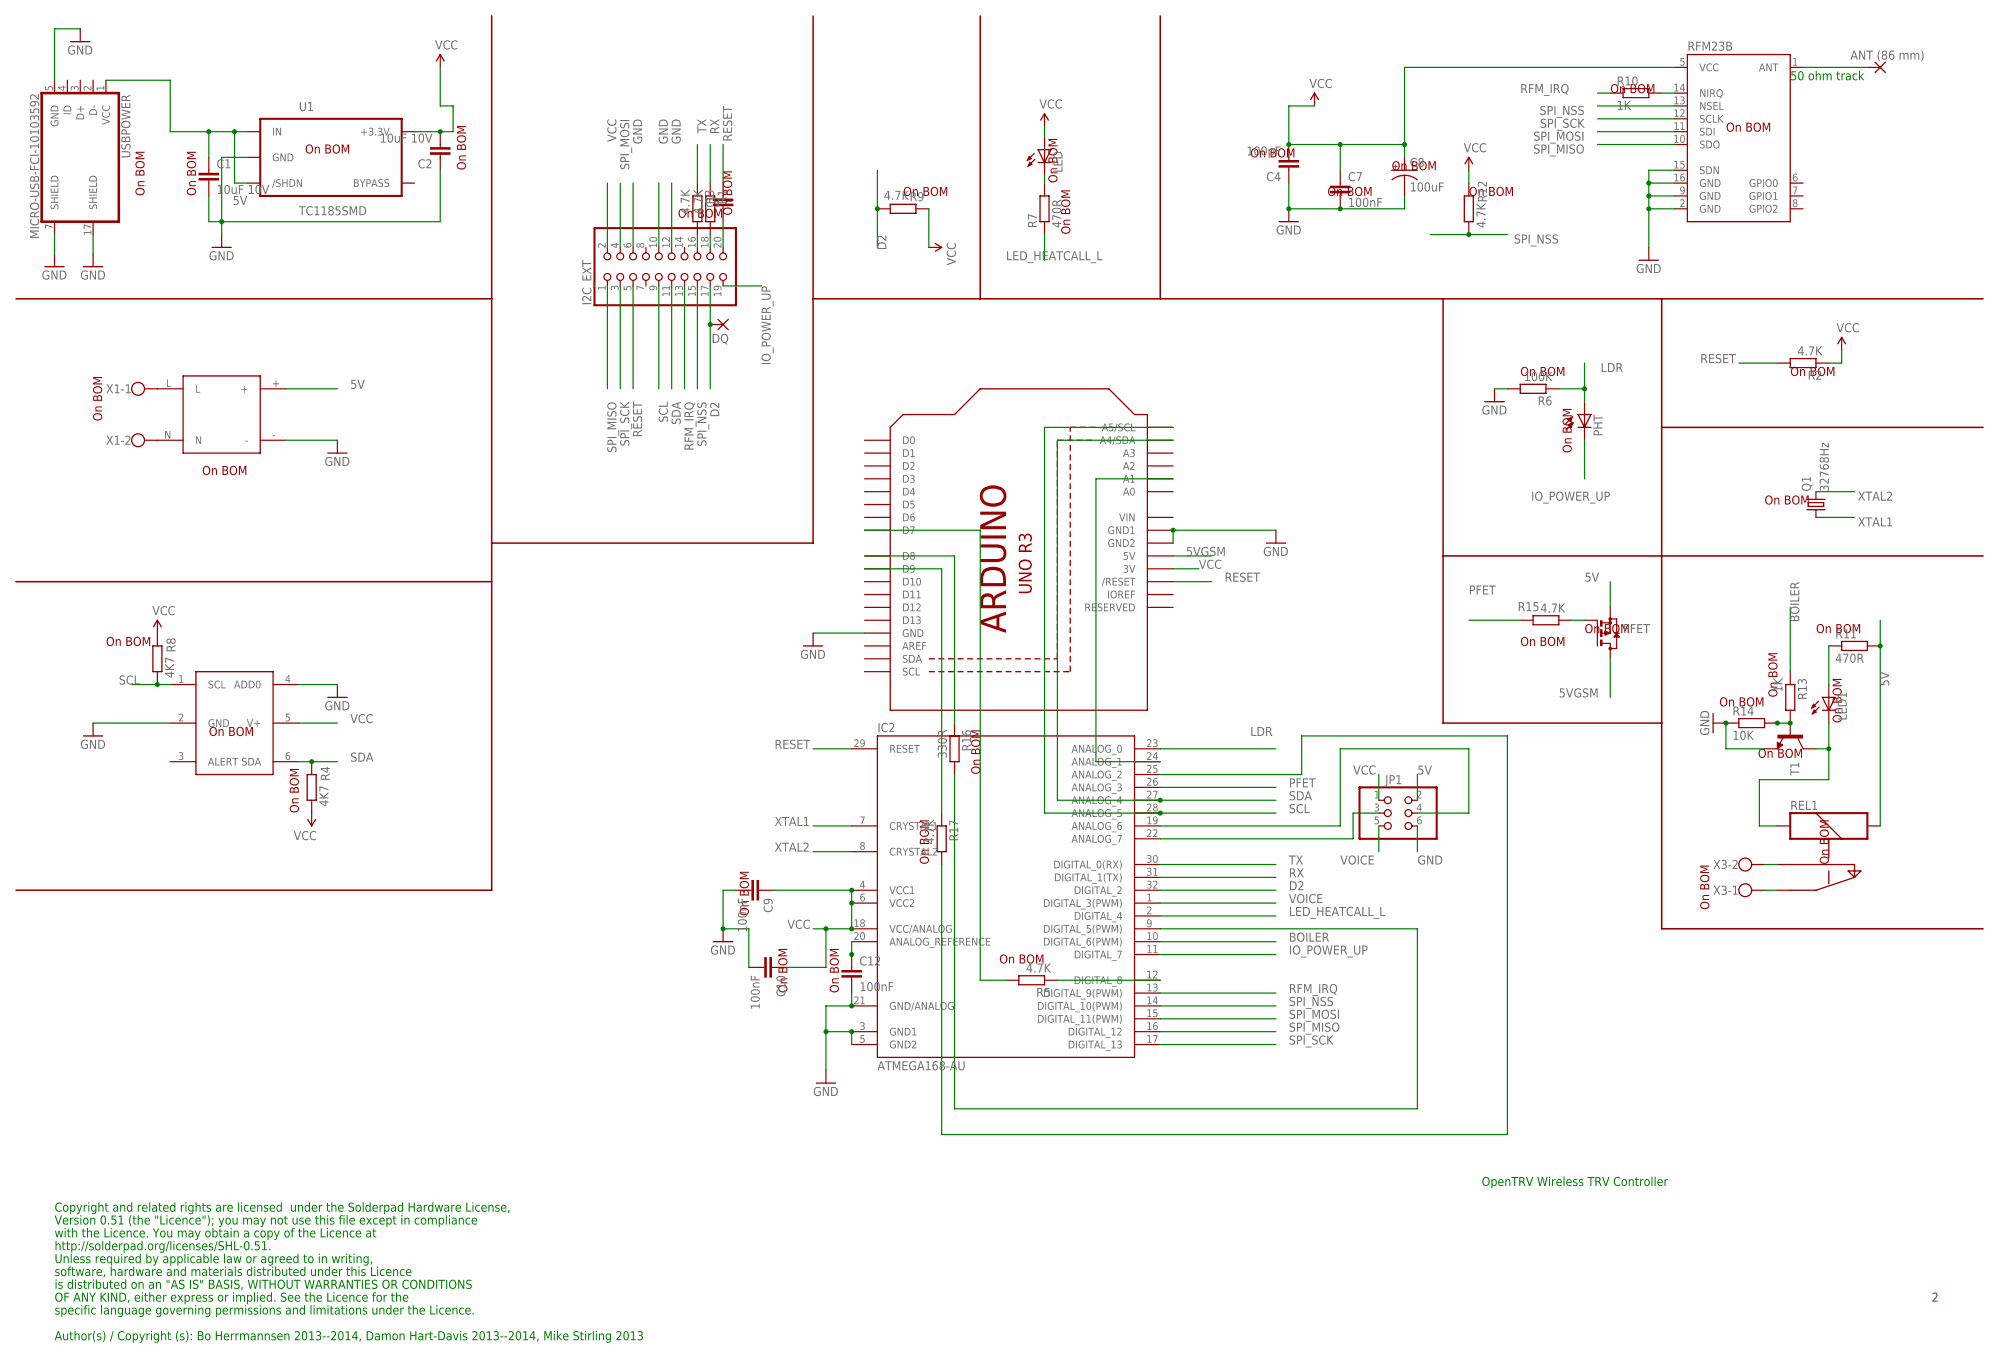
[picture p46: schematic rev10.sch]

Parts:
ANT1: ANT (86 mm); 2,15/1,0
C1, C2: 10uF 10V; C0603
C4: 100pF; C0603
C5, C7, C9, C10, C12: 100nF; C0603
C8: 100uF; EIA3216
DQ: 2,15/1,0
I2C_EXT: PINHD-2X10; 2X10
IC2: ATMEGA168-AU; TQFP32-08
JP1: PINHD-2X3; 2X03
LED, LED1: LEDCHIP-LED0603; CHIP-LED0603
PFET: BSS84; SOT23
PHT: BPX65
PSU: VTX-214-010-205
Q1: 32768Hz; MC-306
R1, R2, R3, R5, R9, R12, R15, R17: 4.7K; R0603
R4, R8: 4K7; R0603
R6: 100K; R0603
R7, R11: 470R; R0603
R10, R13: 1K; R0603
R14: 10K; R0603
R16: 330R; R0603
REL1: OJE-SS-103HM
RFM23B: RFM23B; RFM23-XXX-S1
T1: MMBTH24LT1-NPN-SOT23-BEC; SOT23-BEC
TMP112: TMP1; TMP112
U1: TC1185SMD; TC1185
U$3: ARDUINO
USBPOWER: MICRO-USB-FCI-10103592
X1, X3: W237-102

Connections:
5V: C1.1, JP1.2, PFET.2 (S), PSU.+, R11.2, REL1.S2, U1.1 (IN), U1.3 (/SHDN), USBPOWER.1 (VCC)
5VGSM: PFET.3 (D), U$3.5V
BOILER: IC2.10 (DIGITAL_6(PWM)), R13.1
D2: DQ.1, I2C_EXT.17, IC2.32 (DIGITAL_2), R9.1
GND: C1.2, C2.1, C4.1, C7.2, C8.C (-), C9.2, C10.2, C12.2, I2C_EXT.6, I2C_EXT.10, I2C_EXT.12, IC2.3 (GND1), IC2.5 (GND2), IC2.21 (GND/ANALOG), JP1.6, PSU.-, R6.2, R14.1, RFM23B.2 (GND), RFM23B.9 (GND), RFM23B.15 (SDN), RFM23B.16 (GND), T1.E, TMP112.2 (GND), TMP112.4 (ADD0), U1.2 (GND), U$3.GND, U$3.GND1, U$3.GND2, USBPOWER.5 (GND), USBPOWER.7 (SHIELD), USBPOWER.17 (SHIELD)
IO_POWER_UP: I2C_EXT.19, IC2.11 (DIGITAL_7), PHT.K (C)
LDR: IC2.23 (ANALOG_0), PHT.A, R6.1
LED_HEATCALL_L: IC2.2 (DIGITAL_4), R7.1
unnamed: IC2.19 (ANALOG_6), JP1.4
unnamed: IC2.12 (DIGITAL_8), R5.1
unnamed: PSU.N, X1.2
unnamed: IC2.22 (ANALOG_7), JP1.3
unnamed: C12.1, IC2.20 (ANALOG_REFERENCE)
unnamed: R10.2, RFM23B.14 (NIRQ)
unnamed: PSU.L, X1.1
unnamed: IC2.25 (ANALOG_2), R17.2
unnamed: R13.2, R14.2, T1.B
unnamed: LED.C, R7.2
unnamed: LED1.C, REL1.S1, T1.C
unnamed: IC2.24 (ANALOG_1), U$3.A1
unnamed: LED1.A, R11.1
unnamed: PFET.1 (G), R15.1
unnamed: R5.2, U$3.D7
unnamed: IC2.9 (DIGITAL_5(PWM)), R16.2
unnamed: REL1.C, X3.1
unnamed: REL1.S, X3.2
unnamed: I2C_EXT.18, R1.2
unnamed: I2C_EXT.16, R3.2
unnamed: C5.2, I2C_EXT.20
unnamed: R17.1, U$3.D9
unnamed: ANT1.1, RFM23B.1 (ANT)
unnamed: R16.1, U$3.D8
PFET: IC2.26 (ANALOG_3), R15.2
RESET: C5.1, I2C_EXT.5, IC2.29 (RESET), R2.2, U$3.RESET (/RESET)
RFM_IRQ: I2C_EXT.13, IC2.13 (DIGITAL_9(PWM)), R10.1
RX: IC2.31 (DIGITAL_1(TX)), R1.1
SCL: I2C_EXT.9, IC2.28 (ANALOG_5), R8.1, TMP112.1 (SCL), U$3.A5 (A5/SCL)
SDA: I2C_EXT.11, IC2.27 (ANALOG_4), R4.2, TMP112.6 (SDA), U$3.A4 (A4/SDA)
SPI_MISO: I2C_EXT.1, IC2.16 (DIGITAL_12), RFM23B.10 (SDO)
SPI_MOSI: I2C_EXT.4, IC2.15 (DIGITAL_11(PWM)), RFM23B.11 (SDI)
SPI_NSS: I2C_EXT.15, IC2.14 (DIGITAL_10(PWM)), R12.1, RFM23B.13 (NSEL)
SPI_SCK: I2C_EXT.3, IC2.17 (DIGITAL_13), RFM23B.12 (SCLK)
TX: IC2.30 (DIGITAL_0(RX)), R3.1
VCC: C2.2, C4.2, C7.1, C8.A (+), C9.1, C10.1, I2C_EXT.2, IC2.4 (VCC1), IC2.6 (VCC2), IC2.18 (VCC/ANALOG), JP1.1, LED.A, R2.1, R4.1, R8.2, R9.2, R12.2, RFM23B.5 (VCC), TMP112.5 (V+), U1.5 (+3.3V), U$3.3V
VIN: U$3.VIN
VOICE: IC2.1 (DIGITAL_3(PWM)), JP1.5
XTAL1: IC2.7 (CRYSTAL1), Q1.1
XTAL2: IC2.8 (CRYSTAL2), Q1.4 (2)

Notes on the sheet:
Copyright and related rights are licensed under the Solderpad Hardware License,
Version 0.51 (the "Licence"); you may not use this file except in compliance
with the Licence. You may obtain a copy of the Licence at
http://solderpad.org/licenses/SHL-0.51.
Unless required by applicable law or agreed to in writing,
software, hardware and materials distributed under this Licence
is distributed on an "AS IS" BASIS, WITHOUT WARRANTIES OR CONDITIONS
Author(s) / Copyright (s): Bo Herrmannsen 2013--2014, Damon Hart-Davis 2013--2014, Mike Stirling 2013
OpenTRV Wireless TRV Controller
OF ANY KIND, either express or implied. See the Licence for the
specific language governing permissions and limitations under the Licence.
50 ohm track
On BOM

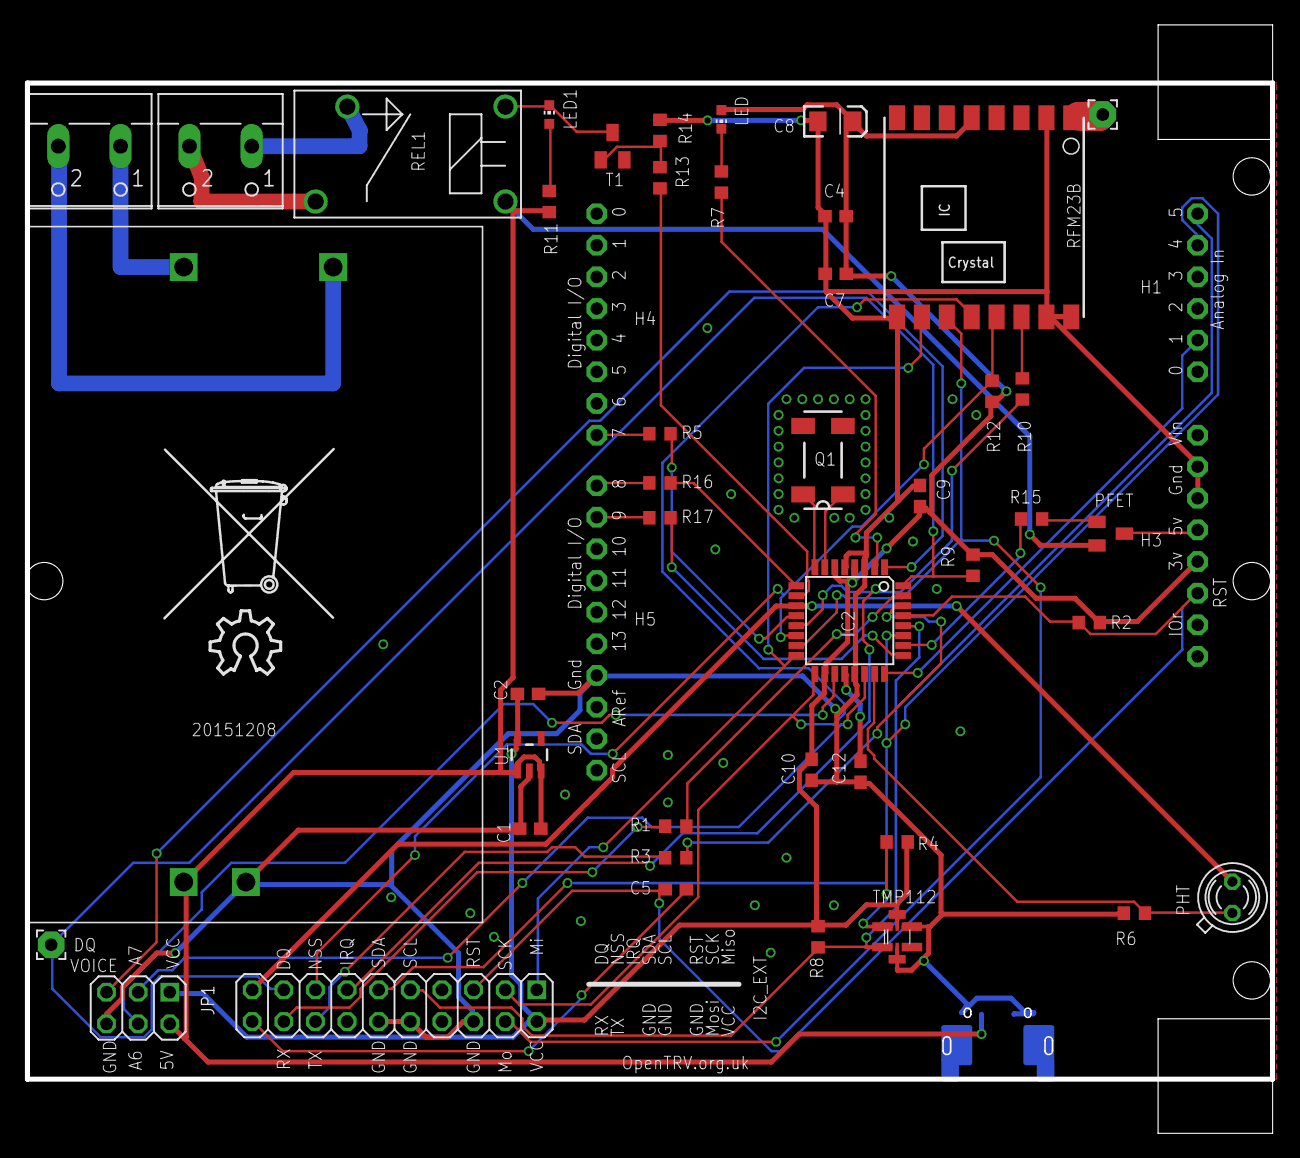
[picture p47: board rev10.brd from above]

Board: 2 copper layers, 100.0 x 80.0 mm, 48 parts (1 on the bottom side), 47 nets.

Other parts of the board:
U$1: OSHW_10X200_NOTEXT
U$2: TONNE

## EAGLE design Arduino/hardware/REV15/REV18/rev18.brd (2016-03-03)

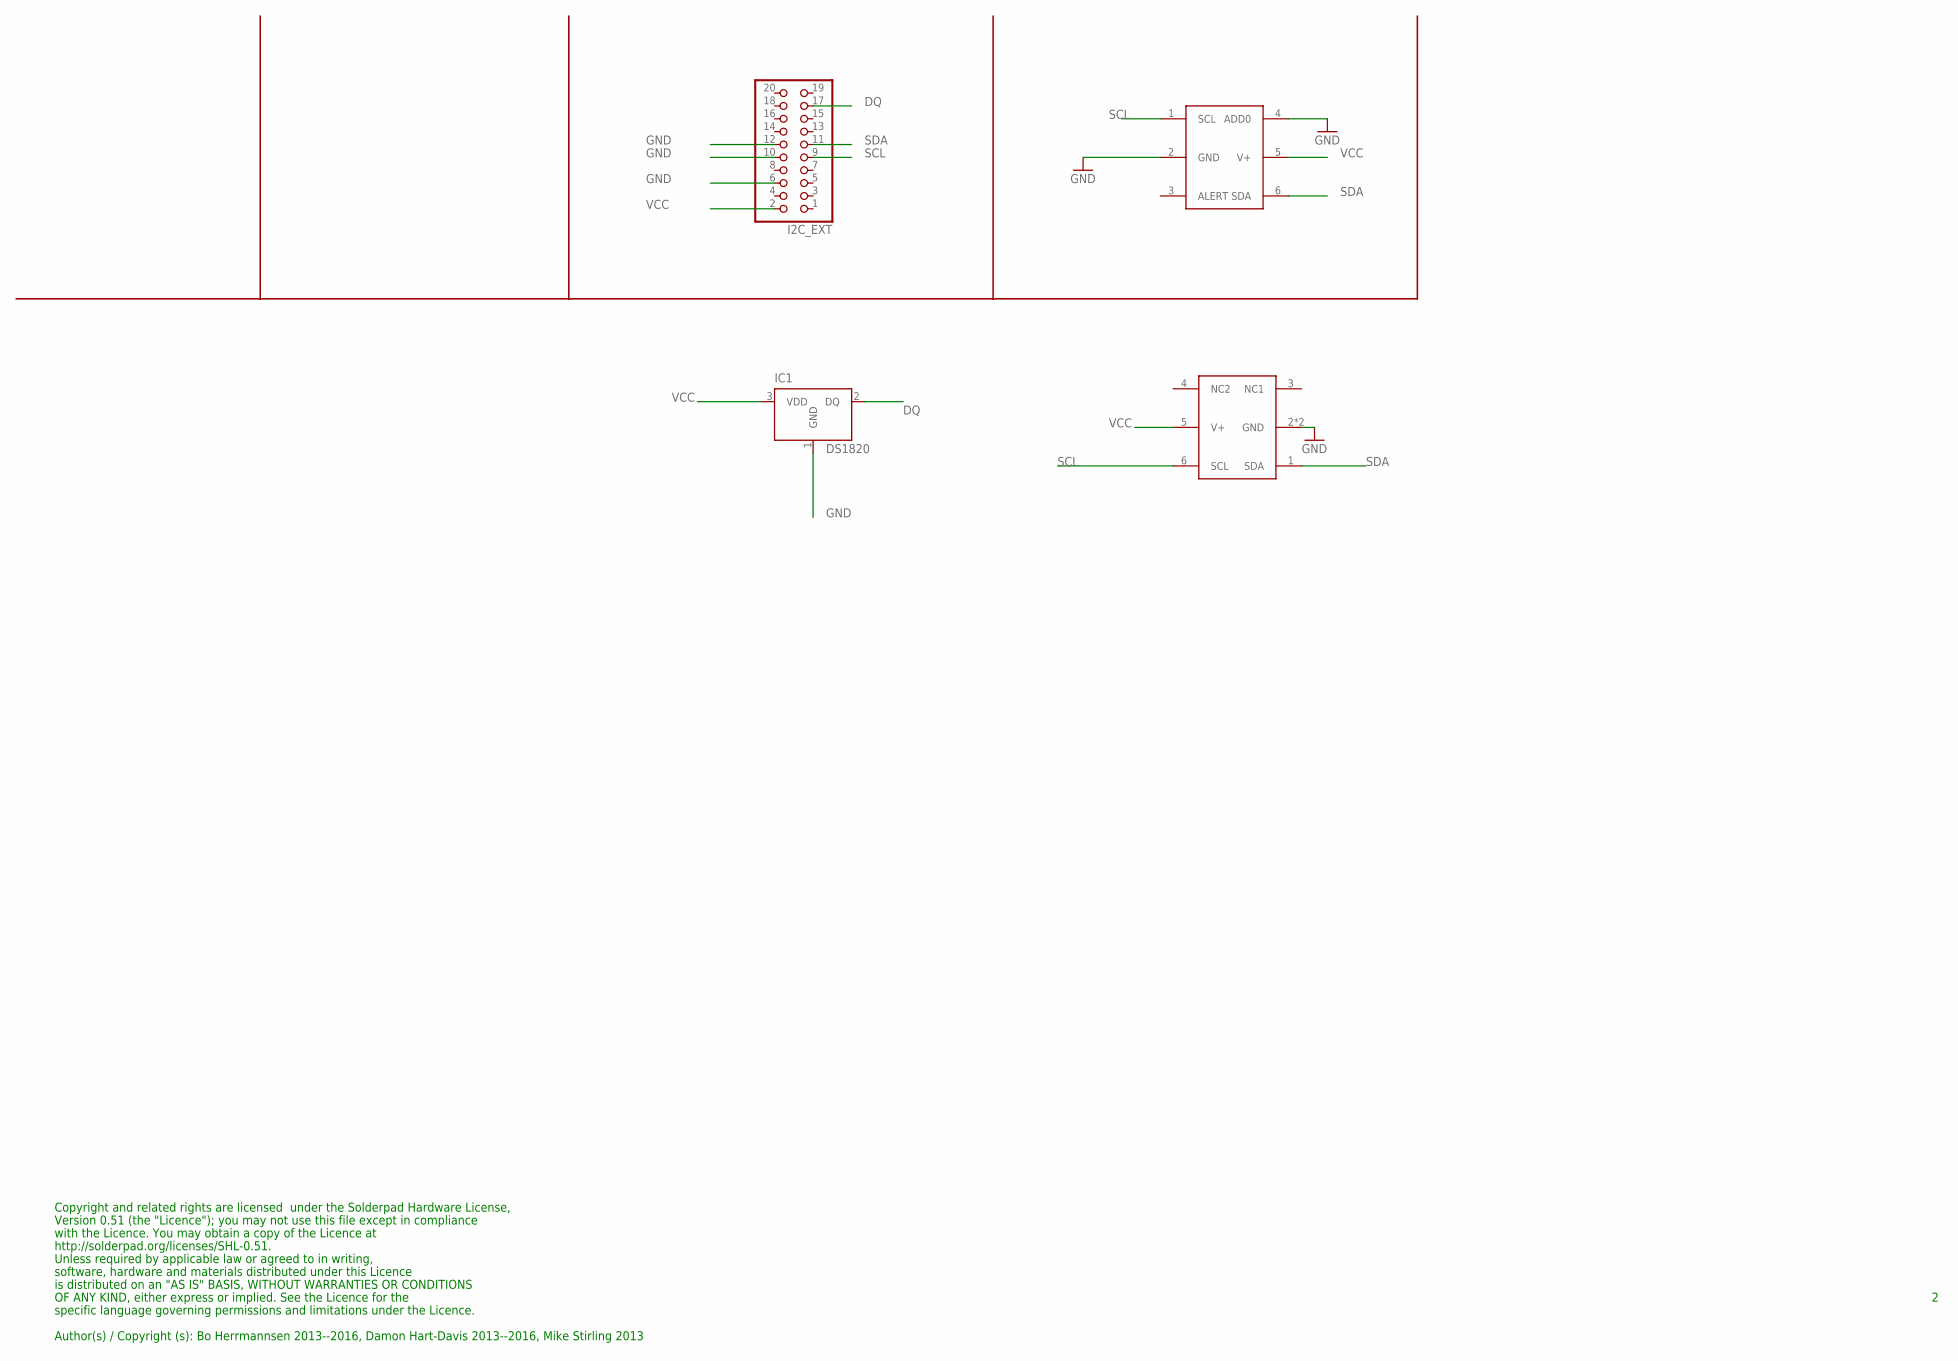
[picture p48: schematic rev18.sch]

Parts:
I2C_EXT: PINHD-2X10; 2X10
IC1: DS1820; TO-92
TMP112: TMP1; TMP112
U$4: SHT21

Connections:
DQ: I2C_EXT.17, IC1.2 (DQ)
GND: I2C_EXT.6, I2C_EXT.10, I2C_EXT.12, IC1.1 (GND), TMP112.2 (GND), TMP112.4 (ADD0), U$4.2 (GND), U$4.P$1 (GND)
SCL: I2C_EXT.9, TMP112.1 (SCL), U$4.6 (SCL)
SDA: I2C_EXT.11, TMP112.6 (SDA), U$4.1 (SDA)
VCC: I2C_EXT.2, IC1.3 (VDD), TMP112.5 (V+), U$4.5 (V+)

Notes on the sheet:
Copyright and related rights are licensed under the Solderpad Hardware License,
Version 0.51 (the "Licence"); you may not use this file except in compliance
with the Licence. You may obtain a copy of the Licence at
http://solderpad.org/licenses/SHL-0.51.
Unless required by applicable law or agreed to in writing,
software, hardware and materials distributed under this Licence
is distributed on an "AS IS" BASIS, WITHOUT WARRANTIES OR CONDITIONS
Author(s) / Copyright (s): Bo Herrmannsen 2013--2016, Damon Hart-Davis 2013--2016, Mike Stirling 2013
OF ANY KIND, either express or implied. See the Licence for the
specific language governing permissions and limitations under the Licence.

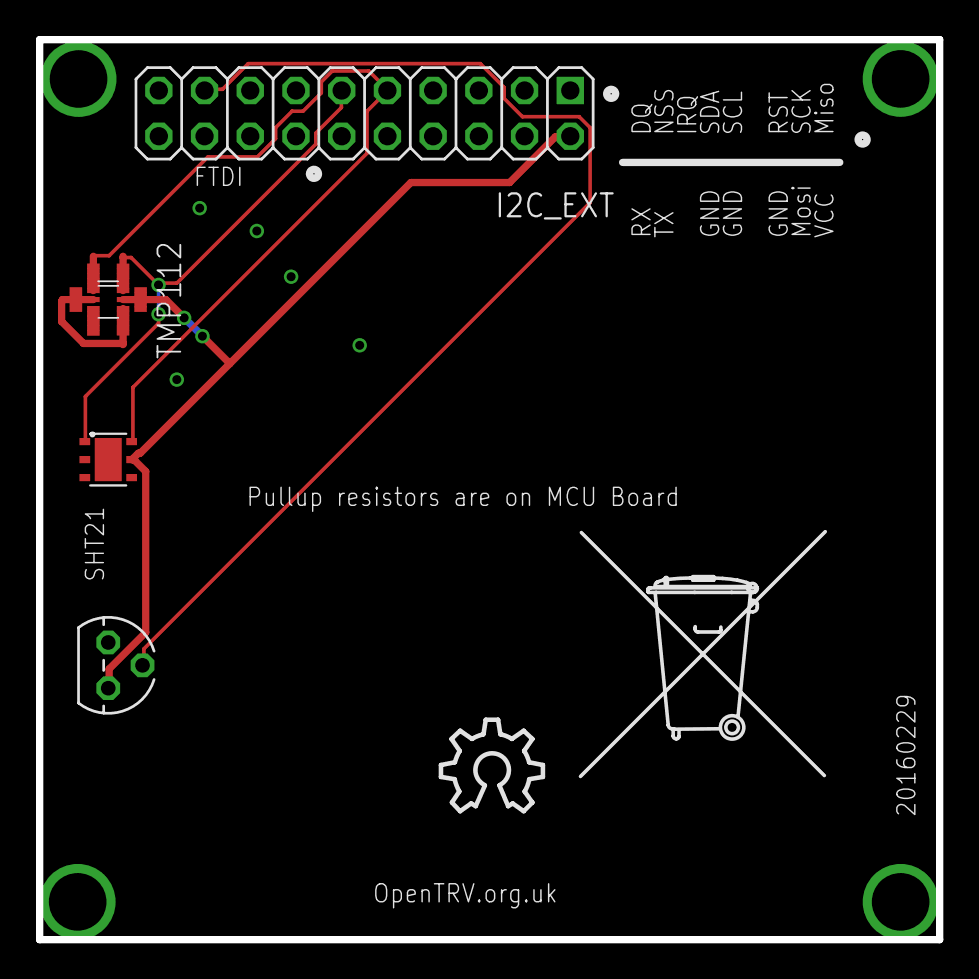
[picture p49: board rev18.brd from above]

Board: 2 copper layers, 50.0 x 50.0 mm, 6 parts (0 on the bottom side), 5 nets.

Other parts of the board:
U$1: OSHW_10X200_NOTEXT
U$2: TONNE

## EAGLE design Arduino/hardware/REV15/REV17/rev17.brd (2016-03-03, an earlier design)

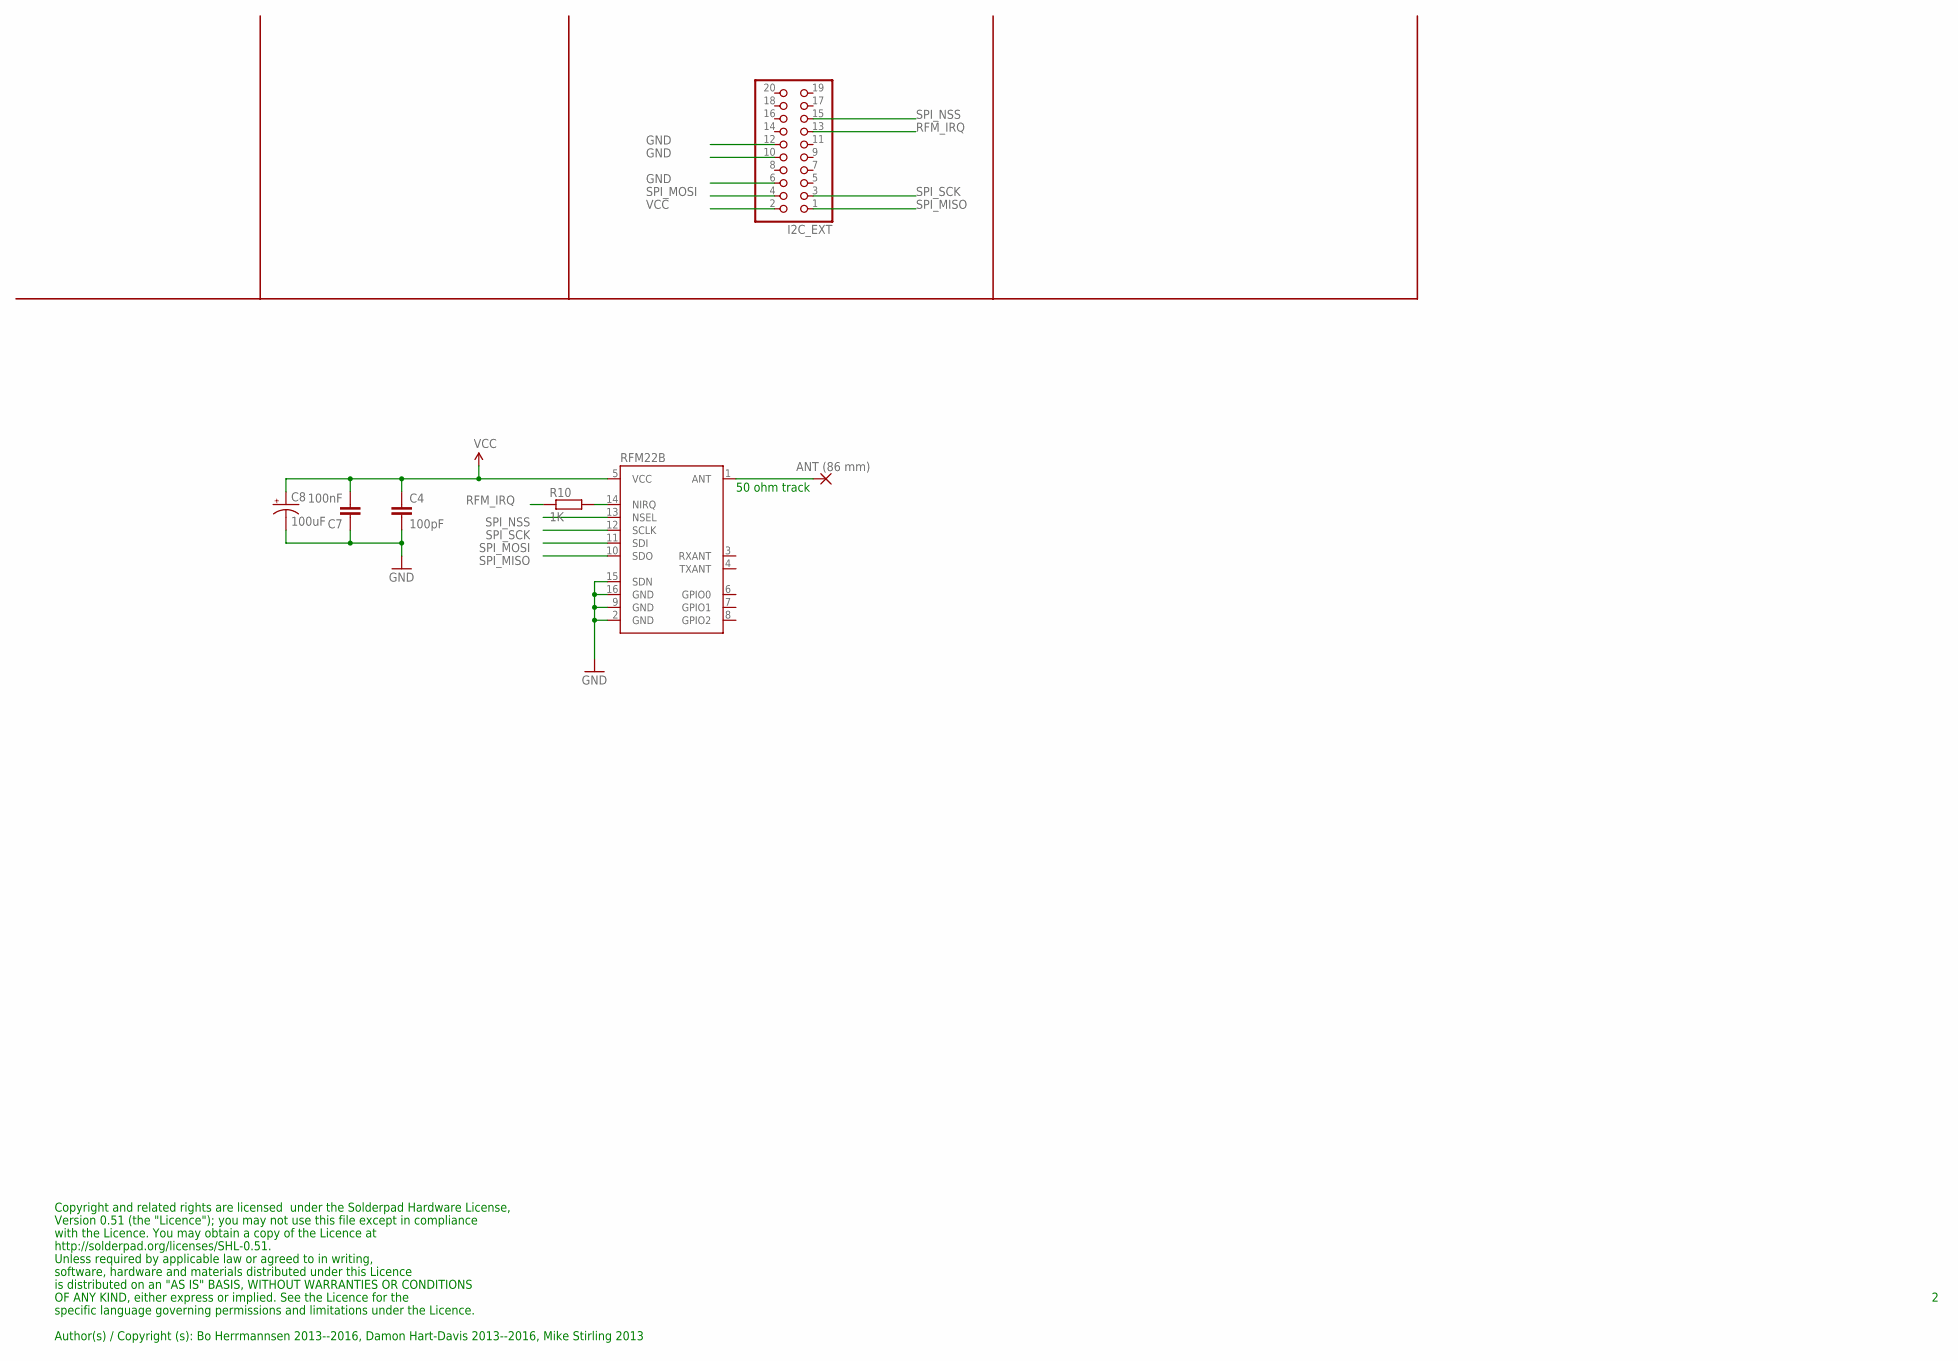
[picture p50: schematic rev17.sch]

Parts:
ANT: ANT (86 mm); 2,15/1,0
C4: 100pF; 0603-CAP
C7: 100nF; 0603-CAP
C8: 100uF; EIA3216
I2C_EXT: PINHD-2X10; 2X10
R10: 1K; R0603
RFM22B: RFM22SMD; RFM22-XXX-S2

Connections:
GND: C4.2, C7.1, C8.C (-), I2C_EXT.6, I2C_EXT.10, I2C_EXT.12, RFM22B.2 (GND), RFM22B.9 (GND), RFM22B.15 (SDN), RFM22B.16 (GND)
unnamed: R10.2, RFM22B.14 (NIRQ)
unnamed: ANT.1, RFM22B.1 (ANT)
RFM_IRQ: I2C_EXT.13, R10.1
SPI_MISO: I2C_EXT.1, RFM22B.10 (SDO)
SPI_MOSI: I2C_EXT.4, RFM22B.11 (SDI)
SPI_NSS: I2C_EXT.15, RFM22B.13 (NSEL)
SPI_SCK: I2C_EXT.3, RFM22B.12 (SCLK)
VCC: C4.1, C7.2, C8.A (+), I2C_EXT.2, RFM22B.5 (VCC)

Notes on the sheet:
Copyright and related rights are licensed under the Solderpad Hardware License,
Version 0.51 (the "Licence"); you may not use this file except in compliance
with the Licence. You may obtain a copy of the Licence at
http://solderpad.org/licenses/SHL-0.51.
Unless required by applicable law or agreed to in writing,
software, hardware and materials distributed under this Licence
is distributed on an "AS IS" BASIS, WITHOUT WARRANTIES OR CONDITIONS
Author(s) / Copyright (s): Bo Herrmannsen 2013--2016, Damon Hart-Davis 2013--2016, Mike Stirling 2013
OF ANY KIND, either express or implied. See the Licence for the
specific language governing permissions and limitations under the Licence.
50 ohm track

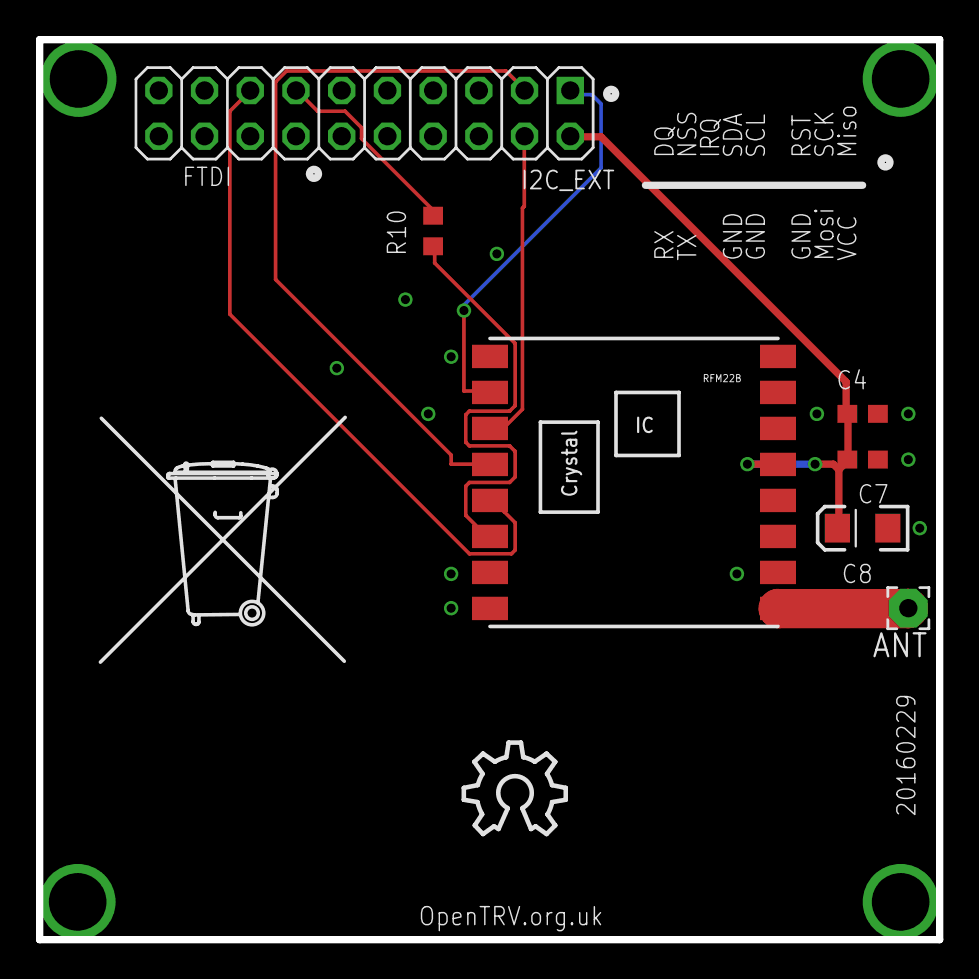
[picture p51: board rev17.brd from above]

Board: 2 copper layers, 50.0 x 50.0 mm, 9 parts (0 on the bottom side), 9 nets.

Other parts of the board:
U$1: OSHW_10X200_NOTEXT
U$2: TONNE

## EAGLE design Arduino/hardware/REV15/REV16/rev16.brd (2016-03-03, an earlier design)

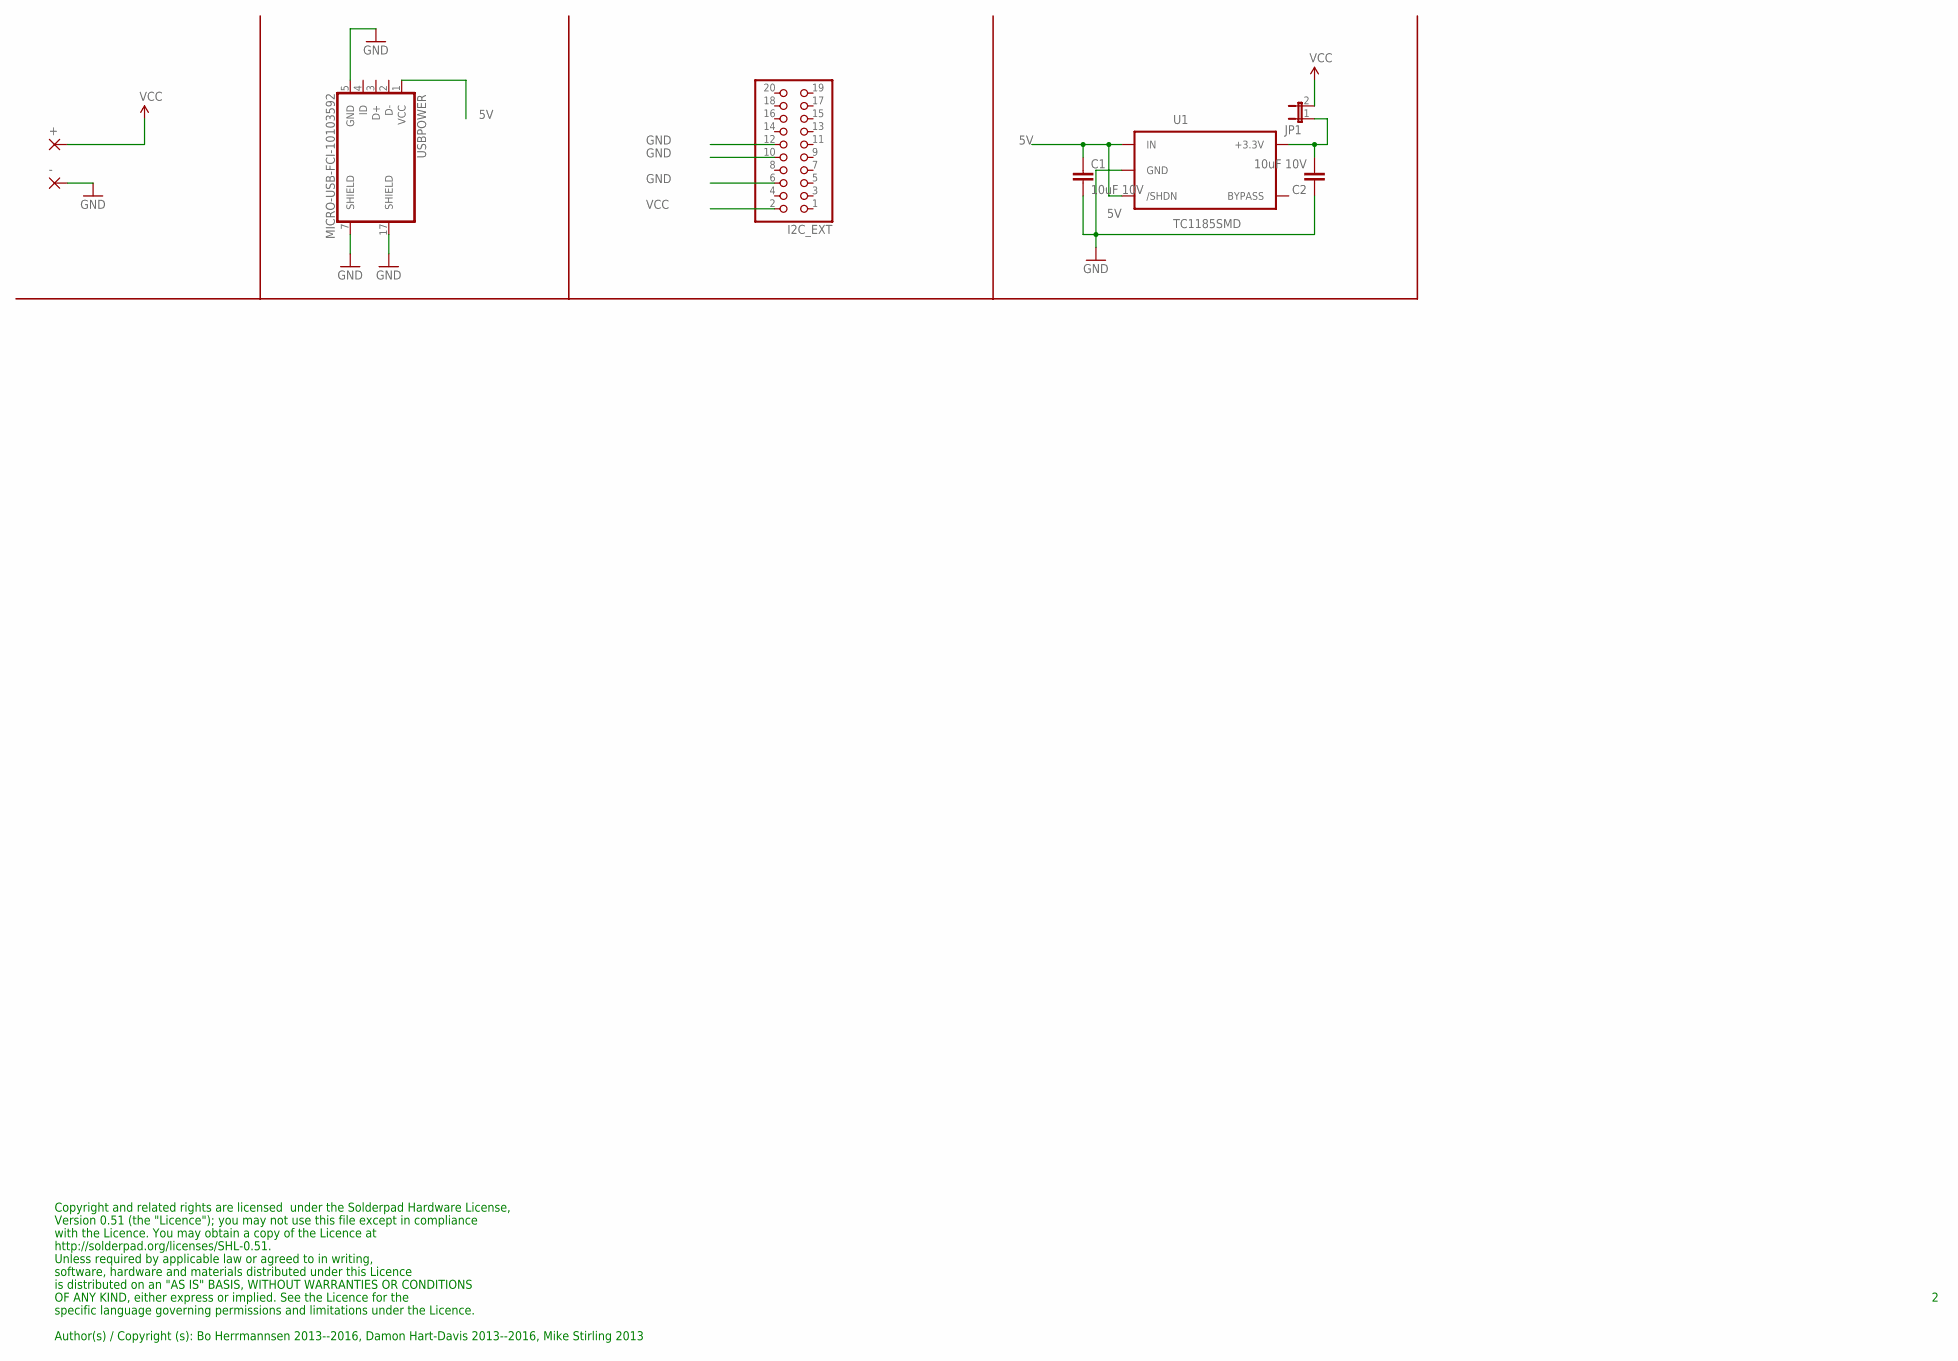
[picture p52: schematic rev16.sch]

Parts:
+: 2,15/1,0
-: 2,15/1,0
C1, C2: 10uF 10V; 0603-CAP
I2C_EXT: PINHD-2X10; 2X10
JP1: JP1E; JP1
U1: TC1185SMD; TC1185
USBPOWER: MICRO-USB-FCI-10103592

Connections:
5V: C1.1, U1.1 (IN), U1.3 (/SHDN), USBPOWER.1 (VCC)
GND: -.1, C1.2, C2.1, I2C_EXT.6, I2C_EXT.10, I2C_EXT.12, U1.2 (GND), USBPOWER.5 (GND), USBPOWER.7 (SHIELD), USBPOWER.17 (SHIELD)
unnamed: C2.2, JP1.1, U1.5 (+3.3V)
VCC: +.1, I2C_EXT.2, JP1.2

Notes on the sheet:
Copyright and related rights are licensed under the Solderpad Hardware License,
Version 0.51 (the "Licence"); you may not use this file except in compliance
with the Licence. You may obtain a copy of the Licence at
http://solderpad.org/licenses/SHL-0.51.
Unless required by applicable law or agreed to in writing,
software, hardware and materials distributed under this Licence
is distributed on an "AS IS" BASIS, WITHOUT WARRANTIES OR CONDITIONS
Author(s) / Copyright (s): Bo Herrmannsen 2013--2016, Damon Hart-Davis 2013--2016, Mike Stirling 2013
OF ANY KIND, either express or implied. See the Licence for the
specific language governing permissions and limitations under the Licence.

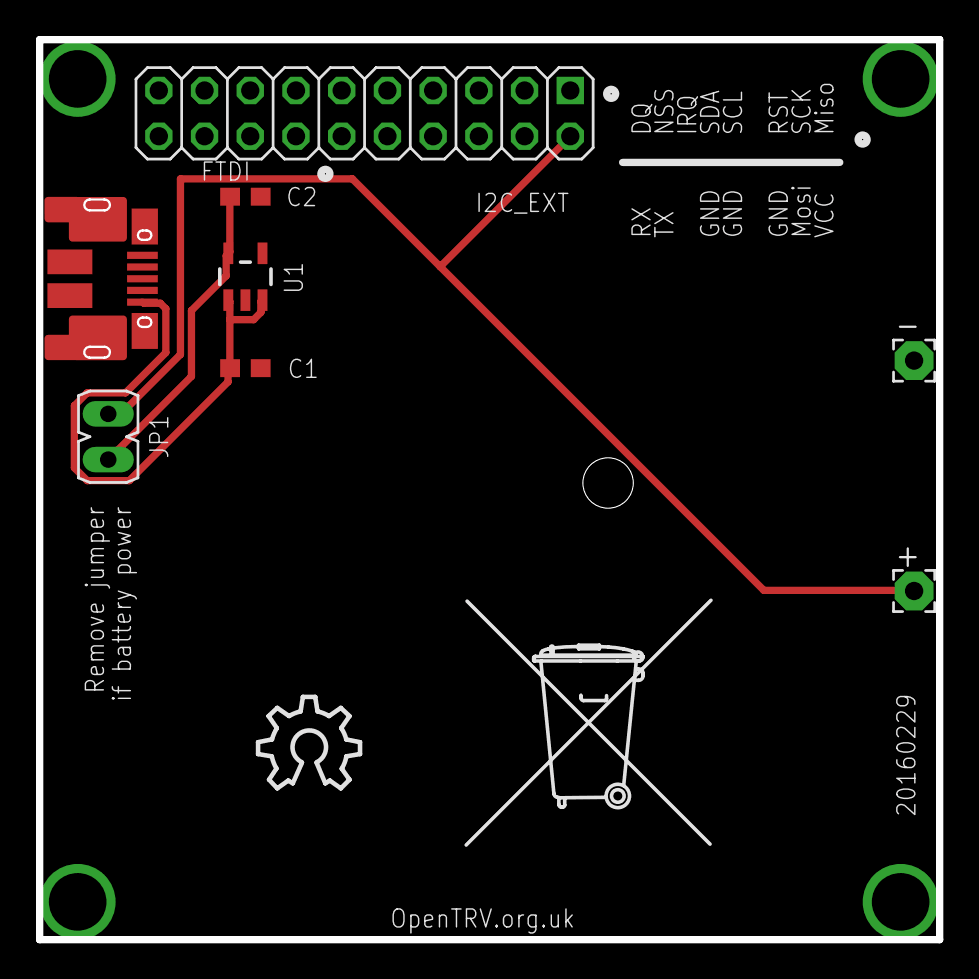
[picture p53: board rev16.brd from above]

Board: 2 copper layers, 50.0 x 50.0 mm, 10 parts (0 on the bottom side), 4 nets.

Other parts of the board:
U$1: OSHW_10X200_NOTEXT
U$2: TONNE

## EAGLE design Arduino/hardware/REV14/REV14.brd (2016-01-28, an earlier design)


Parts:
+: 2,15/1,0
-: 2,15/1,0
C1: 1µ; 0603-CAP
C2: 10µ; C0603
C3, C6: 22pF; C0603
C4: 100n; C0603
C5, C9, C10, C11, C12: 100nF; C0603
C7: 0.22uF; C050H075X075
C8: 100uF; C1206
C13: 0.1uF; C0603
DQ: 2,15/1,0
FTDI_RN2483: PINHD-1X6; 1X06
I2C_EXT: PINHD-2X10; 2X10
IC1: LTC3525; SC70
IC2: ATMEGA168-AU; TQFP32-08
IC3: TS1003IG5TMF; TS1003IG5T
JP2: PINHD-1X10; 1X10
JP3: PINHD-1X6; 1X06
JP4: PINHD-1X4; 1X04
L1: 10 µH; 1210
PAD1, PAD2, PAD3: 2,15/1,0
PHT: BPX65
Q1: 32768Hz; MC-306
R1, R20: 100K; R0603
R2, R3, R4, R5, R6, R7, R8, R9, R10, R11, R12, R13, R14, R15, R16, R17, R18: 4.7K; R0603
R19, R21: 2.2M; R0603
TP1: TPB1,27; B1,27
TP3: TPSQTP07R; TP07R
U1: RN2483
U2: TMP112
U$4: SHT21

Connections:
CHG_PUMP: IC1.1 (SHDN), IC2.26 (ANALOG_3)
D2: DQ.1, I2C_EXT.17, IC2.32 (DIGITAL_2), R9.1
GND: -.1, C1.2, C2.2, C4.2, C6.2, C8.2, C9.2, C10.2, C12.2, C13.2, FTDI_RN2483.1, I2C_EXT.6, I2C_EXT.10, IC1.2 (GND1), IC1.5 (GND2), IC2.3 (GND1), IC2.5 (GND2), IC2.21 (GND/ANALOG), IC3.2 (V-), JP3.1, JP4.3, R1.2, R17.2, R18.1, R20.2, U1.1 (GND), U1.8 (GND), U1.11 (GND), U1.20 (GND), U1.21 (GND), U1.22 (GND), U1.24 (GND), U1.26 (GND), U1.27 (GND), U1.28 (GND), U1.33 (GND), U1.41 (GND), U1.47 (GND), U2.2 (GND), U2.4 (ADD0), U$4.2 (GND), U$4.P$1 (GND)
IO_POWER_UP: I2C_EXT.19, IC2.11 (DIGITAL_7), PHT.A
LDR: IC2.23 (ANALOG_0), PHT.K (C), R1.1
unnamed: I2C_EXT.18, R3.2
unnamed: C11.2, FTDI_RN2483.6
unnamed: I2C_EXT.16, R4.2
unnamed: C5.2, I2C_EXT.20
unnamed: FTDI_RN2483.4, R7.2
unnamed: C12.1, IC2.20 (ANALOG_REFERENCE)
unnamed: FTDI_RN2483.5, R5.2
unnamed: IC2.9 (DIGITAL_5(PWM)), R10.2
unnamed: IC2.12 (DIGITAL_8), R11.2
unnamed: IC1.6 (SW), L1.2
unnamed: IC2.19 (ANALOG_6), R12.2
unnamed: IC2.22 (ANALOG_7), R13.2
unnamed: IC2.25 (ANALOG_2), R14.2
unnamed: FTDI_RN2483.2, R17.1
unnamed: JP4.2, R16.1
unnamed: I2C_EXT.12, R18.2
unnamed: C3.1, PAD1.1
unnamed: C3.2, C6.1, C7.2, IC3.4 (-IN), R21.1
unnamed: C7.1, C8.1, IC3.3 (+IN), R19.2, R20.1
unnamed: PAD2.1, TP1.TP, U1.23 (RFH)
unnamed: PAD3.1, TP3.TP, U1.25 (RFL)
PHONE: C13.1, IC2.24 (ANALOG_1), IC3.1 (OUT), R16.2, R21.2
RESET: C5.1, I2C_EXT.5, IC2.29 (RESET), R2.2
RFM_IRQ: I2C_EXT.13, IC2.13 (DIGITAL_9(PWM))
RN2483_RESET: C11.1, R14.1, R15.2, U1.32 (RESET)
RN2483_UART_CTS: R12.1, U1.3 (UART_CTS)
RN2483_UART_RTS: R13.1, U1.2 (UART_RTS)
RN2483_UART_RX: R7.1, R10.1, U1.7 (UART_RX)
RN2483_UART_TX: R5.1, R11.1, U1.6 (UART_TX)
RX: IC2.31 (DIGITAL_1(TX)), R3.1
SCL: I2C_EXT.9, IC2.28 (ANALOG_5), JP2.1, R8.1, U2.1 (SCL), U$4.6 (SCL)
SDA: I2C_EXT.11, IC2.27 (ANALOG_4), JP2.2, R6.2, U2.6 (SDA), U$4.1 (SDA)
SPI_MISO: I2C_EXT.1, IC2.16 (DIGITAL_12)
SPI_MOSI: I2C_EXT.4, IC2.15 (DIGITAL_11(PWM))
SPI_NSS: I2C_EXT.15, IC2.14 (DIGITAL_10(PWM))
SPI_SCK: I2C_EXT.3, IC2.17 (DIGITAL_13)
TX: IC2.30 (DIGITAL_0(RX)), R4.1
VCC: +.1, C1.1, C4.1, C9.1, C10.1, I2C_EXT.2, IC1.3 (VIN), IC2.4 (VCC1), IC2.6 (VCC2), IC2.18 (VCC/ANALOG), IC3.5 (V+), JP4.4, L1.1, R2.1, R6.1, R8.2, R9.2, R15.1, R19.1, U1.12 (3.3V), U1.34 (3.3V), U2.5 (V+), U$4.5 (V+)
VCC1: C2.1, IC1.4 (VOUT), JP3.3, JP4.1
VOICE_NIRQ: IC2.10 (DIGITAL_6(PWM)), JP2.8
XTAL1: IC2.8 (CRYSTAL2), Q1.4 (2)
XTAL2: IC2.7 (CRYSTAL1), Q1.1

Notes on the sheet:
VOICE MODULE - on BOM - Locked
Crystal - on BOM - Locked
AVR Reset Pullup - on BOM - Locked
Battery Connection - on BOM - Locked
DS18B20 Pullup - on BOM - Locked
Light Sensor - on BOM - Locked
I2C_EXT Connector - on BOM - Locked
TMP112 + SHT21 +I2C Pullup's - on BOM - Locked
Charge Pump - on BOM - Locked
LoRa MODULE - on BOM - Locked
Programming for LoRa MODULE - on BOM - Locked
Mobile Detector MODULE - on BOM - Locked
Do NOT Pop
Copyright and related rights are licensed under the Solderpad Hardware License,
Version 0.51 (the "Licence"); you may not use this file except in compliance
with the Licence. You may obtain a copy of the Licence at
http://solderpad.org/licenses/SHL-0.51.
Unless required by applicable law or agreed to in writing,
software, hardware and materials distributed under this Licence
is distributed on an "AS IS" BASIS, WITHOUT WARRANTIES OR CONDITIONS
OF ANY KIND, either express or implied. See the Licence for the
specific language governing permissions and limitations under the Licence.


Board: 2 copper layers, 100.0 x 50.0 mm, 57 parts (0 on the bottom side), 47 nets.

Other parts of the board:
U$1: OSHW_10X200_NOTEXT

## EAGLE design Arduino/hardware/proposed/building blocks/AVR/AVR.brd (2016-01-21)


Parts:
C5, C9, C10, C12: 100nF; C0603
DQ: 2,15/1,0
I2C_EXT: PINHD-2X10; 2X10
IC2: ATMEGA168-AU; TQFP32-08
PAD1, PAD2, PAD3, PAD4, PAD5, PAD6, PAD7, PAD8, PAD9, PAD10, PAD11, PAD12, PAD13, PAD14, PAD15, PAD16, PAD17, PAD18, PAD19, PAD20, PAD21, PAD22, PAD23, PAD24, PAD25: 1,6/0,8
Q1: 32768Hz; MC-306
R2, R3, R4, R6, R8, R9: 4.7K; R0603

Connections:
D2: DQ.1, I2C_EXT.17, IC2.32 (DIGITAL_2), PAD14.1, R9.1
GND: C9.2, C10.2, C12.2, I2C_EXT.6, I2C_EXT.10, I2C_EXT.12, IC2.3 (GND1), IC2.5 (GND2), IC2.21 (GND/ANALOG), PAD2.1
IO_POWER_UP: I2C_EXT.19
unnamed: I2C_EXT.18, R3.2
unnamed: IC2.23 (ANALOG_0), PAD4.1
unnamed: I2C_EXT.16, R4.2
unnamed: C5.2, I2C_EXT.20
unnamed: IC2.24 (ANALOG_1), PAD5.1
unnamed: C12.1, IC2.20 (ANALOG_REFERENCE)
unnamed: IC2.25 (ANALOG_2), PAD6.1
unnamed: IC2.19 (ANALOG_6), PAD10.1
unnamed: IC2.1 (DIGITAL_3(PWM)), PAD15.1
unnamed: IC2.2 (DIGITAL_4), PAD16.1
unnamed: IC2.9 (DIGITAL_5(PWM)), PAD17.1
unnamed: IC2.10 (DIGITAL_6(PWM)), PAD18.1
unnamed: IC2.11 (DIGITAL_7), PAD19.1
unnamed: IC2.26 (ANALOG_3), PAD7.1
unnamed: IC2.22 (ANALOG_7), PAD11.1
unnamed: IC2.12 (DIGITAL_8), PAD20.1
RESET: C5.1, I2C_EXT.5, IC2.29 (RESET), PAD1.1, R2.2
RFM_IRQ: I2C_EXT.13, IC2.13 (DIGITAL_9(PWM)), PAD21.1
RX: IC2.31 (DIGITAL_1(TX)), PAD13.1, R3.1
SCL: I2C_EXT.9, IC2.28 (ANALOG_5), PAD9.1, R8.1
SDA: I2C_EXT.11, IC2.27 (ANALOG_4), PAD8.1, R6.2
SPI_MISO: I2C_EXT.1, IC2.16 (DIGITAL_12), PAD24.1
SPI_MOSI: I2C_EXT.4, IC2.15 (DIGITAL_11(PWM)), PAD23.1
SPI_NSS: I2C_EXT.15, IC2.14 (DIGITAL_10(PWM)), PAD22.1
SPI_SCK: I2C_EXT.3, IC2.17 (DIGITAL_13), PAD25.1
TX: IC2.30 (DIGITAL_0(RX)), PAD12.1, R4.1
VCC: C9.1, C10.1, I2C_EXT.2, IC2.4 (VCC1), IC2.6 (VCC2), IC2.18 (VCC/ANALOG), PAD3.1, R2.1, R6.1, R8.2, R9.2
XTAL1: IC2.8 (CRYSTAL2), Q1.4 (2)
XTAL2: IC2.7 (CRYSTAL1), Q1.1

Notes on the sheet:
On BOM
Crystal
AVR Reset Pullup
DS18B20 Pullup
I2C_EXT Connector
I2C Pullup's


Board: 2 copper layers, 36.8 x 30.9 mm, 39 parts (0 on the bottom side), 31 nets.

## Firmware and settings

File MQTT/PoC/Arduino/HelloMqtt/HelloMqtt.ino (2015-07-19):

#include <SPI.h>
#include <Ethernet.h>
#include "PubSubClient.h"

const unsigned int BAUD_RATE = 9600;

// Update these with values suitable for your network.
byte mac[]    = { 0x90, 0xA2, 0xDA ,0x0D, 0x2A, 0xC6 };
byte server[] = { 192, 168, 0, 6 };
byte my_ip[]  = { 192, 168, 0, 7 };

void callback(char* topic, byte* payload, unsigned int length) {
  // handle message arrived
}

EthernetClient ethClient;
PubSubClient client(server, 1883, callback, ethClient);

void setup()
{
  Serial.begin(BAUD_RATE);
  Ethernet.begin(mac, my_ip);
}

void loop()
{
  delay(1000);
  Serial.print("Connecting...");
  if (client.connect("ArduinoClient")) {
    client.publish("Sample/Arduino","Hello Arduino");
    Serial.println("Published to MQTT.");
  } else {
    Serial.println("Failed to publish.");
  }
  client.disconnect();
}

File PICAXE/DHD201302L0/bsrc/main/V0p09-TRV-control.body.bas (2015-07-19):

; *************************************************************
;
; The OpenTRV project licenses this file to you
; under the Apache Licence, Version 2.0 (the "Licence");
; you may not use this file except in compliance
; with the Licence. You may obtain a copy of the Licence at
;
; http://www.apache.org/licenses/LICENSE-2.0
;
; Unless required by applicable law or agreed to in writing,
; software distributed under the Licence is distributed on an
; "AS IS" BASIS, WITHOUT WARRANTIES OR CONDITIONS OF ANY
; KIND, either express or implied. See the Licence for the
; specific language governing permissions and limitations
; under the Licence.
;
; *************************************************************
; Author(s) / Copyright (c): Damon Hart-Davis 2013

; TRV (and boiler-node) body including control loop for DHD201203 level-0 spec on V0.09 PCB1 hardware.

; A #picaxe and #define CONFIG_... should have been defined textually above this in the .bas file,
; and the I/O pin definitions and any preliminary 'safe' initialisation also.

; See end for TODO and RECENT CHANGES.

#no_end ; Main loop is non-terminating, so save a few bytes!



;-----------------------------------------
; UI DESCRIPTION
; Button causes cycling through 'off'/'frost' target of 5C, 'warm' target of ~18C,
; and an optional 'bake' mode that raises the target temperature to up to ~24C
; for up to ~30 minutes or until the target is hit then reverts to 'warm' automatically.
; (Button may have to be held down for up to a few seconds to get the unit's attention.)
; Acknowledgement is medium/long/double flash in new mode
; (medium is frost, long is 'warm', long+medium is 'bake').

; Without the button pressed,
; the unit generates one to three short flashes on a two-second cycle if in heat mode.
; A first flash indicates "warm mode".  (This first flash will be lengthened if a schedule is set.) 
; A second flash if present indicates "calling for heat".
; A third flash if present indicates "bake mode" (which is automatically cancelled after a short time, or if the high target is hit).

; This may optionally support an interactive CLI over the serial connection,
; with reprogramming initiation permitted (instead of CLI) while the UI button is held down.

; If target is not being met then aim to turn TRV on/up and call for heat from the boiler too,
; else if target is being met then turn TRV off/down and stop calling for heat from the boiler.
; Has a small amount of hysteresis to reduce short-cycling of the boiler.
; Does some proportional TRV control as target temperature is neared to reduce overshoot.

; This can use a simple setback (drops the 'warm' target a little to save energy)
; eg using an LDR, ie reasonable ambient light, as a proxy for occupancy.



;-----------------------------------------
; PRE-DEFINED CONFIG_... IMPLEMENTATION/EXPANSION

#ifdef CONFIG_DHD_STUDY ; DHD's study with TRV.
; IF DEFINED: this unit supports CLI over the USB/serial connection, eg for run-time reconfig.
;#define SUPPORT_CLI
; IF DEFINED: this unit supports BAKE mode.
#define SUPPORT_BAKE
; IF DEFINED: this unit may run on 2xAA cells, preferably rechargeable eg NiMH, ~2V--2.4V, and should monitor supply voltage with calibadc.
;#define SUPPLY_VOLTAGE_LOW_2AA ; May require limiting clock speed and using some alternative peripherals/sensors...
; IF DEFINED: this unit will act as boiler-control hub listening to remote thermostats, possibly in addition to controlling a local TRV.
;#define BOILER_HUB
; IF DEFINED: this unit will act as a thermostat controlling a local TRV (and calling for heat from the boiler).
#define LOCAL_TRV
symbol FHT8V_HC1 = 13 ; House code 1, constant or (byte) register.
symbol FHT8V_HC2 = 73 ; House code 2, constant or (byte) register.
; IF DEFINED: RFM23 is in use in place of RFM22.
#define RFM22_IS_ACTUALLY_RFM23 ; RFM23 used on V0.09 PCB1.
; IF DEFINED: good RF environment means that TX power level can be reduced.
#define RFM22_GOOD_RF_ENV ; Good ground-plane and antenna: drop TX level.
; IF DEFINED: use simple LDR-based detection of room use/occupancy; brings in getRoomInUseFromLDR subroutine.
#define USE_MODULE_LDROCCUPANCYDETECTION
; If LDR is not to be used then specifically define OMIT_... as below.
;#define OMIT_MODULE_LDROCCUPANCYDETECTION ; LDR 'occupancy' sensing irrelevant for DHW.
; IF DEFINED: use DS1306 RTC for accurate elapsed time measures at least.
#define USE_MODULE_DS1306RTCSPISIMPLE
; IF DEFINED: use MCP79410 RTC (with I2C).
;#define USE_MODULE_MCP79410_RTC_SIMPLE
; IF DEFINED: produce regular status reports on sertxd.
;#define SERTXD_STATUS_REPORTS
; IF DEFINED: use active-low LEARN button.  Needs SUPPORT_SINGLETON_SCHEDULE.
;#define LEARN_BUTTON_AVAILABLE ; OPTIONAL ON V0.09 PCB1
;symbol BUTTON_LEARN_L = input5 ; C.5 ; Low when "LEARN" button pressed.
; IF DEFINED: support one on and one off time per day (possibly in conjunction with 'learn' button).
; Test simple schedule to warm in evening from 9pm to 10pm.
;#define SUPPORT_SINGLETON_SCHEDULE
;symbol DEFAULT_SINGLETON_SCHEDULE_ON = $ff ; No default on.
;symbol DEFAULT_SINGLETON_SCHEDULE_OFF = $ff ; No default off.
#endif

#ifdef CONFIG_DHD_KITCHEN ; DHD's kitchen with TRV, which also contains the boiler.
;#define SUPPORT_CLI
#define SUPPORT_BAKE
#define BOILER_HUB
#define LOCAL_TRV
symbol FHT8V_HC1 = 45 ; House code 1, constant or (byte) register.
symbol FHT8V_HC2 = 26 ; House code 2, constant or (byte) register.
#define USE_MODULE_LDROCCUPANCYDETECTION
#define USE_MODULE_DS1306RTCSPISIMPLE
#endif

#ifdef CONFIG_DHD_LIVINGROOM ; DHD's living room with TRV.
;#define SUPPORT_CLI
#define SUPPORT_BAKE
#define LOCAL_TRV
symbol FHT8V_HC1 = 10 ; House code 1, constant or (byte) register.
symbol FHT8V_HC2 = 69 ; House code 2, constant or (byte) register.
#define USE_MODULE_LDROCCUPANCYDETECTION
#define LDR_EXTRA_SENSITIVE ; LDR not exposed to much light.
#define USE_MODULE_DS1306RTCSPISIMPLE
#endif
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

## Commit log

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2015-12-14 Fixing up current tests.
2015-12-14 Preliminary dual radio commit
    - Framing issues due to RFM23B framing
    - Startup button tests commented out
    - Comes to ~28 kB with no CLI
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2015-12-17 TODO-664: WIP
    Also killing for now complex and fragile logic
    trying to power down receiver when not
    needed to save energy.
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2015-12-18 TODO-655: relaying correct vanilla JSON stats
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2015-12-19 TODO-664: improved comments
    Also corrected (reduced) upper bound
    on JSON side in secure frame.
2015-12-19 TODO-655: trimming code
    Eliminating UI for non-TRV-controlling boards.
    Saves 424 bytes and some confusion!
2015-12-19 Changes to be committed: modified: SecureFrameTest.java
    First draft of Frame build and decode. Encryption not added yet.
2015-12-20 minor fixes
    Including ensuring UI LED turned off each minor cycle,
    since various bthings can turn it on asynchronously.
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2015-12-27 TODO-688: testing
    Also probably made significant fix in calcs
    for extended ambient light scale.
    Also forcing all UI LEDs off before sampling
    ambient light.
2015-12-27 REV14 initial board and git ignore files
    [REV14.brd, REV14.sch]
2015-12-28 TODO-370: motor reversed
    In sample unit supplied motor direction
    is reverse compared to dev unit.
2015-12-29 TODO-695: speeding UI interaction with dial
    Trying to give near instant response in terms of
    showing when the valve is likely to call for heat
    so the user can tweak it up just until it starts
    to double flash.
2015-12-30 TODO-696: improvement
    Make less prone to problems from temperature history
    companding effects, eg granularity.
2015-12-30 DORM1
    Avoid flashing UI LED most of the time unless
    room is known to be lit (ie default to not flash)
    to save some energy and avoid annoying users
    if lighting is always poor.
2016-01-01 TODO-696: disable for DORM1
    At least on first Shenzhen sample without case on,
    while it seems once to have correctly inferred
    occupancy from RH (from humdity from cooking),
    it is at least as often triggered spuriously
    by an apparent fall in RH% as temperature drops sharply
    as the radiator is turned off.
    So, saving some complexity and code space.
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2016-01-05 updated rev 14
    [REV14.brd, REV14.sch]
2016-01-05 rev 14 ant tracks and xtal done
    [REV14.brd, REV14.sch]
2016-01-05 DORM1 start-up improvement.
    Trying to make CLI marginally more useful
    during valve self-calibration.
2016-01-05 rev14 ready for routing
    [REV14.brd, REV14.sch]
2016-01-05 TODO-697: avoiding polling valve logic AS_SENSOR
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2016-01-06 updated readme...
    2-4 set of docs are confusing.... it makes things far more dificult for
    those that do the work
    [REV14.brd]
2016-01-06 added ftdi for updating LoRa
    [REV14.brd, REV14.sch]
2016-01-06 rev 14 updated and intial routing attempt
    [REV14.brd, REV14.sch]
2016-01-07 Changed addPadding function to always pad to 32 bytes. Previously it would pad to 16 or 32 depending on the length of the plain text. This change increases security by not allowing information on the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
2016-01-07 charge pump added
    [REV14.brd, REV14.sch]
2016-01-08 routed with 1 wire left.
    missing SHT21
    [REV14.brd, REV14.sch]
2016-01-11 reservered space for mobdet on rev 14
    [AVR.brd, AVR.sch, REV14.brd]
2016-01-12 added rough mobdect to rev14
    [REV14.brd, REV14.sch]
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2016-01-14 rev14 prerouting
    [REV14.brd, REV14.sch]
2016-01-14 more ground plane on rev14
    [REV14.brd]
2016-01-14 TODO-723: tightened up 'I' command
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2016-01-15 rev 14 update
    [REV14.brd, REV14.sch]
2016-01-15 rev14 with mobile detect
    [REV14.brd, REV14.sch]
2016-01-15 rev14 routed
    [REV14.brd, REV14.sch]
2016-01-15 rev 14 ready for gerbers
    [REV14.brd, REV14.sch]
2016-01-15 rev 14 really ready now
    [REV14.brd]
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2016-01-16 rev14 without blooper
    [REV14.brd]
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2016-01-16 rev14 pre routing.... again :-D
    [REV14.brd, REV14.sch]
2016-01-16 rev14 routed again
    [REV14.brd, REV14.sch]
2016-01-16 rev14 ground plane fixed
    [REV14.brd]
2016-01-16 fixed cap footprint for mobile detect
    [REV14.brd, REV14.sch]
2016-01-16 REV14 Gerbers update
    [REV14.GBL, REV14.GBO, REV14.GBP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]
2016-01-16 added more stitching to rev14
    [REV14.brd]
2016-01-16 REV14 updated Gerbers with more stitching
    [REV14.GBL, REV14.GTL]
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2016-01-17 REV14: adding CSV copy of BOM
    [BOM.20160117.csv]
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2016-01-18 Fixed pin def typos
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2016-01-20 a few ideas for modular building blocks
    [AVR.brd, AVR.sch, RFM.brd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]
2016-01-21 Added TMP to building blocks folder
    [TMP.brd, TMP.sch]
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2016-01-28 rev14 cut2
    [REV14.brd, REV14.sch]
2016-01-28 rev14 cut2 corrected
    [REV14.brd, REV14.sch]
2016-01-28 REV14 tentative new Gerbers
    [REV14.GBL, REV14.GBS, REV14.GTL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]
2016-01-28 REV14 BOM update
    [BOM.20160128.csv]
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2016-02-11 TODO-787: un-reverse pot for REV7
    Also note that it has ~25% of normal travel,
    biased nearly all to low end,
    at least for first DORM1 full device.
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2016-02-11 Node setting seems to work
    To add a new node: "A hh hh hh hh hh hh hh hh"
    - Reads first two bytes of each token in hex and ignores the rest.
    - Prints number of nodes set to serial
    - Stops adding nodes once EEPROM full
    - No error checking yet.
    - Only accepts upper case for hex values.
    To clear all nodes: "A *"
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2016-02-22 Fixed compilation bug for expand and compress temperature
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2016-02-24 rough rev 15
    [rev10.brd, rev10.sch]
2016-02-25 rev16
    rough power board
    [rev10.brd, rev10.sch]
2016-02-25 files renamed
    [rev15.brd, rev15.sch, rev16.brd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]
2016-02-25 new structure
    [rev16.brd, rev16.sch]
2016-02-26 up to rev18 roughly
    [rev17.brd, rev17.sch, rev18.brd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]
2016-02-26 up to rev18 cleaned up
    [rev15.brd, rev15.sch, rev16.brd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]
2016-02-26 up to rev18 DRC check and ground plane
    [rev15.brd, rev16.brd, rev16.sch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]
2016-02-28 REV15-18 cleaned up, need sanity check
    [rev15.brd, rev15.sch, rev16.brd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]
2016-03-01 rev15-18 changed as per Deniz suggeastions
    [rev15.brd, rev16.brd, rev17.brd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]
2016-03-02 ic2_ext labels closer to connector
    [rev15.brd, rev16.brd, rev17.brd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]
2016-03-03 Added FTDI label to board as per deniz advice
    [rev15.brd, rev16.brd, rev17.brd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]
2016-03-03 Fixed C16 sensor ID
2016-03-03 Added REV15 gerbers + readme etc. Waiting on Bo for BOM
    [rev15.GBL, rev15.GBO, rev15.GBP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]
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2016-03-15 Added Devices model and fixed error in MQTT tests
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2016-04-14 fixed rev10 transistor
    [rev10.brd, rev10.sch]
2016-04-15 Disabling initial CLI activation on boot.
    Avoids stealing time from other things at startup
    such as valve calibration.
    CLI can be activated with any character on the input line.
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2016-05-17 ETV test case data samples 2016/03 16WW
    [201603-ETV-16WW-sample-HDD15p5-DegreeDaysNet-EGLL.csv, 201603-ETV-16WW-sample-gas-consumption-kWh-Loop-EGLL.csv]
2016-05-20 TODO-897: extra (better) test data set for ETV
    [201602-ETV-16WW-sample-HDD15p5-DegreeDaysNet-EGLL.csv, 201602-ETV-16WW-sample-gas-consumption-kWh-Loop-EGLL.csv]
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2016-06-21 TODO-897: ETV support
    [201602-ETV-16WW-sample-HDD15p5-DegreeDaysNet-EGLL.csv]
2016-07-06 TODO-897: splitting input API ready to process data format as supplied
    [Navetas-data-format-sample.csv]
2016-07-06 TODO-897: WIP
    [N-bulk-data-format-sample.csv]
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2016-07-08 TODO-897: verifying correct sample choice
2016-07-08 TODO-897: testing correct behaviour around DST switch to match HDD
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2016-08-03 TODO-897: HDD data as downloaded
    [2016H1-EGLL_HDD_15.5C.csv]
2016-08-03 TODO-897: format simplified
    [2016H1-EGLL_HDD_15.5C.csv]
2016-08-03 TODO-897: extra data trimmed
    [2016H1-EGLL_HDD_15.5C.csv]
2016-08-03 TODO-897: moving some test data to more appropriate package
    [201602-ETV-16WW-sample-gas-consumption-kWh-Loop-EGLL.csv, 201603-ETV-16WW-sample-gas-consumption-kWh-Loop-EGLL.csv, N-bulk-data-format-sample.csv]
2016-08-03 TODO-897: extended gas kWh sample
    [N-sample-GAS-2016-07.csv]
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2016-08-04 TODO-897: computation TDD
    [N-sample-GAS-2016-06.csv]
2016-08-07 walrus and motor driver eval
    [rev11.brd, rev11.sch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]
2016-08-09 motor eval board as pr deniz request
    [rev11.brd, rev11.sch]
2016-08-12 fixes for Arduino AVR boards v1.6.12

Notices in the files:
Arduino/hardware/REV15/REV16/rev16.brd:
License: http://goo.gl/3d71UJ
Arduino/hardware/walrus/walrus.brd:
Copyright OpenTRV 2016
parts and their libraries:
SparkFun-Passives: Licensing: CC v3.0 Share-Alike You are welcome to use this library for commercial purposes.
